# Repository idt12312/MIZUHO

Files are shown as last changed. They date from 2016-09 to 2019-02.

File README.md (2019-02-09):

# MIZUHOについて
## 概要
マイクロマウスの機体です。  

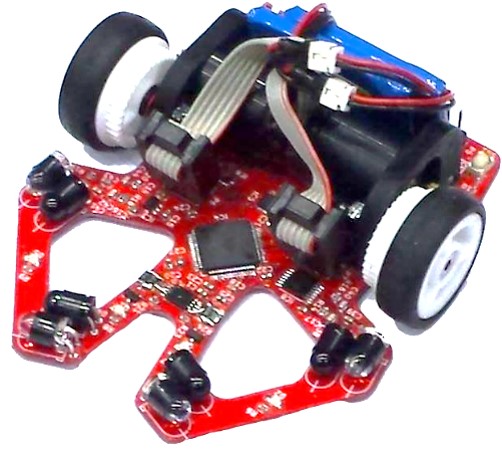
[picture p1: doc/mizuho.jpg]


第37回全日本マイクロマウス大会のクラッシック競技フレッシュマンクラスに出場しました。  
予選を通過し、決勝では11位のタイムで完走しました。

## 使用部品

| | |
|---|---|
| マイコン | STM32F405RGT |
| 6軸センサ | MPU6500 |
| モータドライバ | DRV8835 |
| フォトダイオード | SFH213FA |
| 赤外線LED | VSLY5850 |
| モーター | Faulhaber 1717+IEH2-1024 |
| バッテリー | Hyperion 1cel 120mA × 2  |

# 内容物
* pcb/ : kicadの基板データ
* firmware/ : stm32のファームウェア(eclipseのプロジェクトファイル)

# ファームウェアについて 
## 構成
↓の画像のような構成になっています。

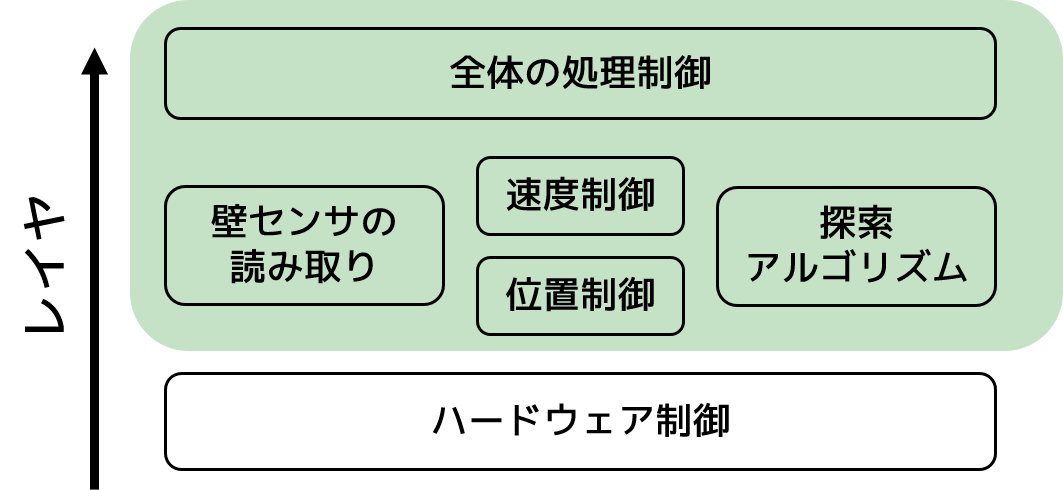
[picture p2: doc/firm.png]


[FreeRTOS](http://www.freertos.org/)を利用しています。  
上の画像の緑の色のついている部分がFreeRTOSのタスクになっています。  

## 制御の概要
だいたいこんな感じです。

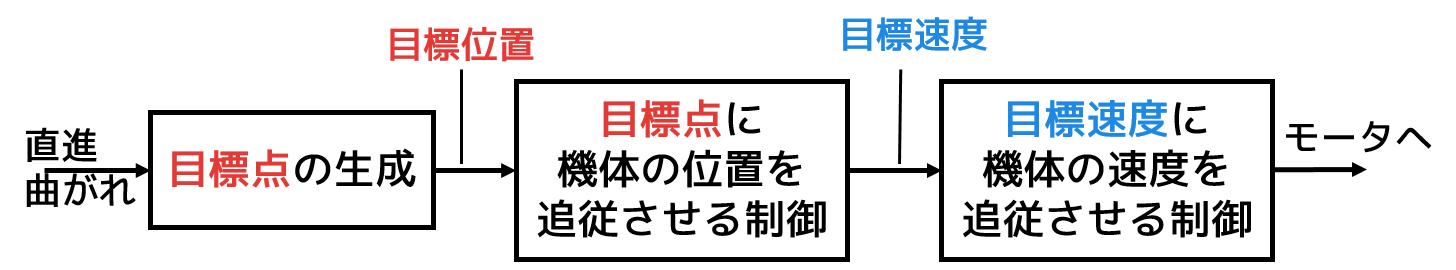
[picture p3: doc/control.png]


## 探索アルゴリズム
[以前作ったもの](https://github.com/idt12312/MazeSolver2015)を使用しています。

# 回路について
[回路図はここからpdfダウンロードできます。](./doc/micromouse2016.pdf)

## 壁センサ
壁センサは少し工夫したので説明しておきます。  
ロ技研内での技術交流のために作成したまとめ文章も置いておくので、よかったら見てください  
[研究報告書](https://github.com/idt12312/MIZUHO/blob/master/doc/docment.pdf)  

外乱を防ぐために赤外線LEDを変調して使っています。

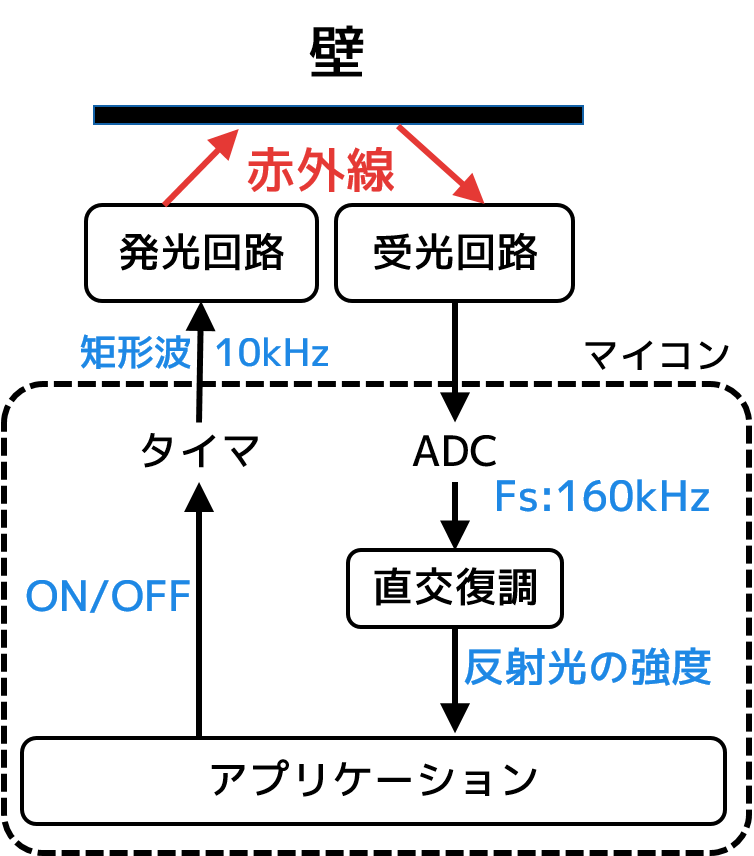
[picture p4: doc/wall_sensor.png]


受光した信号は直交復調に基づいて復調しています。  
計算自体はDFTをとある周波数についてだけ計算することと同じです。  

受光した信号を

、サンプリング周波数を

とします。  
ここでは

から周波数

成分の強度を計算するとします。  

まず

X[n] = \sum_{k=0}^{N-1}x[k]\exp({-j\frac{2 \pi nk}{N}})

を計算します。  

次に

の絶対値を計算することで  

に含まれる周波数

の振幅を得ることができます。

# 開発環境
## 基板
* 基板の外形はinventorで作成 -> dxfで出力
* 回路図・アートワークはKiCad 4.0.4-stableで作成

## STM32
* コンパイラ : GCC 4.9.3 (arm-none-eabi)
* デバッガ : GDB 7.8.0.20150604-cvs (arm-none-eabi)
* OpenOCD 0.9.0
* IDE : Eclipse
  * CDT
  * GNU ARM Eclipse plugin
* eclipseのプロジェクトの雛形はGNU ARM Eclipse pluginから自動生成されるものを使用
* STM32のStandard Peripheral Libraryを使用

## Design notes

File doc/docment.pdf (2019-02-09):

# MIZUHO(マイクロマウス)の開発 ～壁センサの新提案～

Cheese∗ @idt12312

2016.12.5

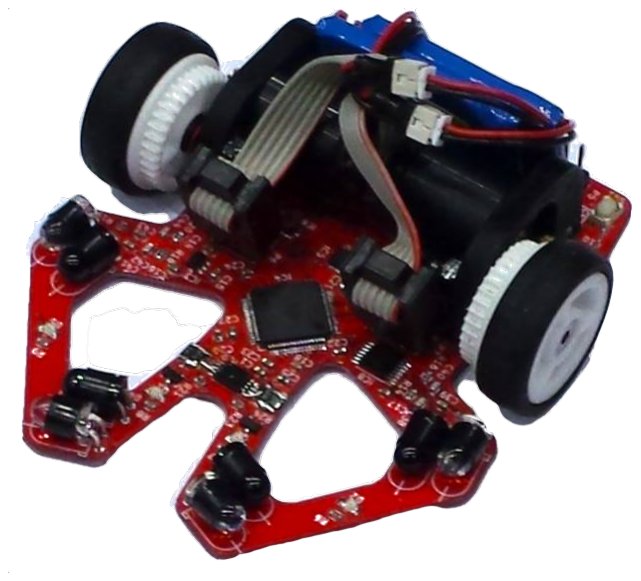
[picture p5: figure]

図 1: MIZUHO の外観

## 1 はじめに

マイクロマウスの競技のため, MIZUHO(図 1) とい う機体を製作した. マイクロマウスの機体の製作は初
めてであるため, 基本的にはよく知られたものを組み合 わせて製作をした. しかし, 唯一壁センサ周りに関して は既存のものを真似るだけではなく, 独自に開発を行っ た. そのため, 本報告書では独自に開発をした壁センサ について述べる.
マイクロマウスにおいて, 壁センサはフィールドに
ある壁の有無や壁との距離を計測するために使われ,
フィールドに対する絶対的な位置情報を取得できる唯
一のセンサである. そのため, 競技発足初期から現在に 至るまで, また初心者から上級者までほとんどの機体で 壁センサは利用されている. しかしネット上でも見ら
れる広く知られている壁センサの構成方法 [2] には後の 章で述べる問題点があるため, 新たな壁センサの構成方 法を開発するに至った.
ちなみに, MIZUHO の開発に関するソースコード, 基板の設計データ (KiCad) は全て github[1] にて公 開をしている. 製作過程や Tips などは id 研ブログ (http://idken.net) で公開をしているので, こちらも参 照していただきたい.

∗ロ技研内のマイクロマウスの機体の製作, 大会への出場を行う研 究室. 2016 年 12 月に設立.

## 2 壁センサの概要

MIZUHO はフィールドの壁情報を取得するために壁 センサを 4 つ搭載している. 左右の壁を見るために 2 つ, 前方の壁を見るために 2 つ搭載している (図 1). マイクロマウスの壁を見るセンサは赤外線 LED を利 用したものが最も一般的である. 赤外線 LED の光を壁 に当て, 反射して返ってくる光量を測定することで壁の 有無・壁との距離を計測することができる. なお, 光量 の計測にはフォトダイオードやフォトトランジスタを
使用されることが多い. しかしこの方法の問題点とし
て, 照明などの周囲の光の影響を受けやすいというもの が挙げられる.
この問題を解決するため, 照射する光を変調するとい
う手法が用いられている. 具体的には赤外線 LED を十 分に高い周波数で点滅させ, LED が ON になっている ときの受光した信号と OFF になっているときに受光し た信号の差をとる [2](以降従来手法と呼ぶ) というもの である. 会場の照明として水銀灯や蛍光灯があり, それ らは数 100Hz で点滅をしているため, 例えば数 kHz の 周波数で変調することで照明の影響を受けなくするこ
とができる. 変調方法として, LED を一定の周波数で 点滅させる方法や単純に LED を短いパルス状に点灯す るという方法が用いられている.
従来手法は信号の振幅を計測する手法であるが, 波形
がなまりすぎている場合や変調した周波数に近い (オー ダーが同じくらい) 外乱がある場合は精度よく計測をす ることができないことが予想される. そこで今回は光
を変調して発光, 受光する回路とその変調された信号の 強度を精度よく算出する方法を提案する.
提案するシステムである壁センサの関連の構成は図
2 のようになっている.
発光回路はマイコンから入力される信号に応じて
LED を点灯する. ここでは部品のばらつきによって 照射強度にばらつきがでない工夫がしてある. 受光回
路では, マイコンでの信号処理の前段階として 1 次の LPF と HPF を施しつつ, 信号を増幅している. マイコ ン内部では, 受光した信号を ADC を通して取り込み, 直交復調を用いることで特定の周波数の強度を算出し

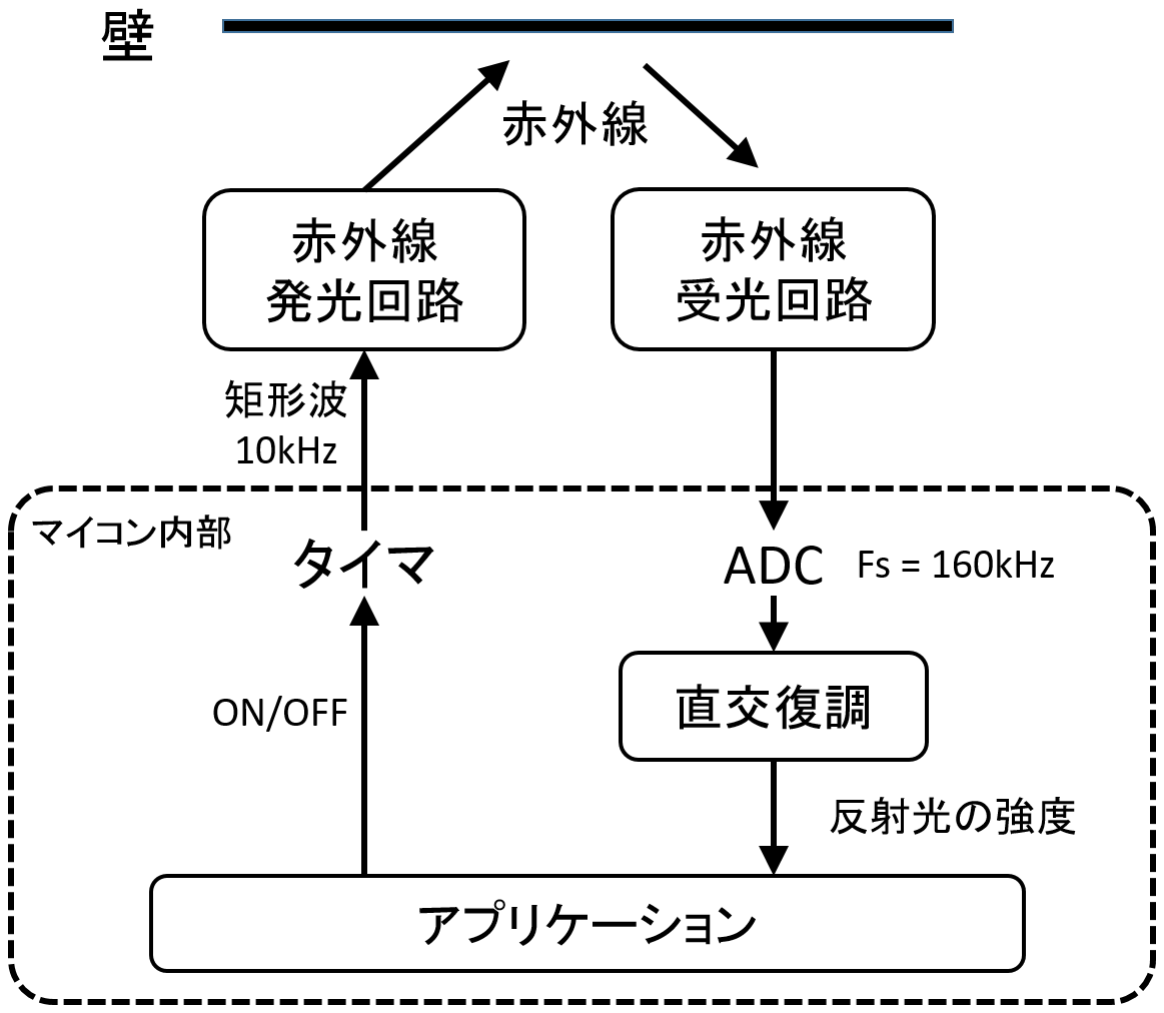
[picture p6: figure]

図 2: 壁センサのシステム構成

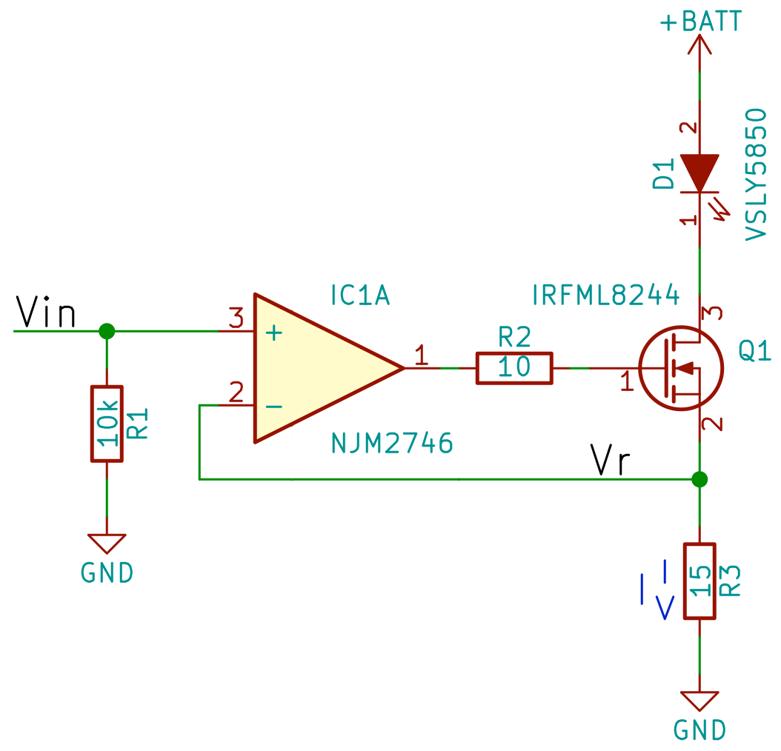
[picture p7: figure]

図 3: 赤外線発光回路

ている.
以降の章では発光回路, 受光回路, 直交復調の詳細に ついて述べる.

## 3 発光回路

MIZUHO の壁センサの発光回路には図 3 の回路を用 いた. この回路はオペアンプ, FET, R3 の抵抗で定電流 回路を構成している. この定電流回路により LED には 一定の電流が流れるため, 電源電圧の変動や LED の順 方向電圧などの部品によるばらつきの影響を受けない
ようにすることができる. なお, 実際には赤外線 LED を 2 個直列にしてこの回路を 2 セット用いて実装して いる.
LED に流れる電流はオペアンプの入力電圧 Vin に よってアナログ的に変化させることができる. オペア
ンプによって Vr = Vin になるように FET が駆動され るので, R3 には常に Vin の電圧が印加される. FET の ドレインからゲートにはほとんど電流が流れないため,
LED に流れる電流 I は

I =

V in
R3

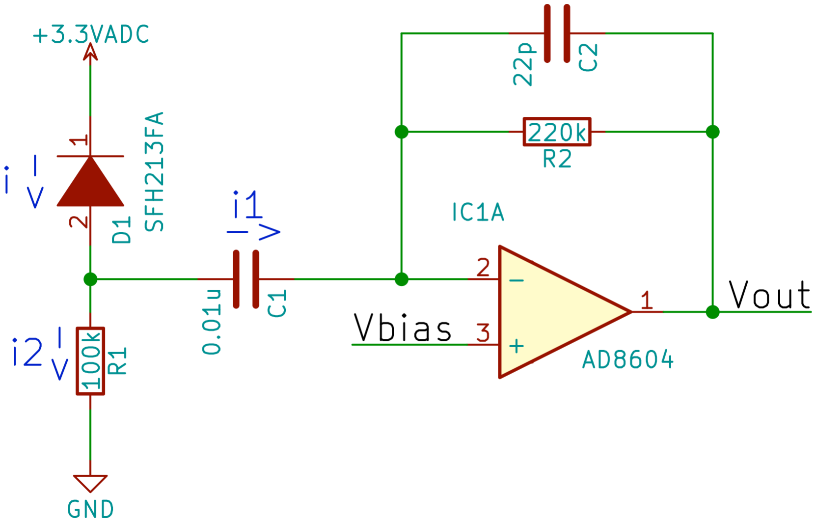
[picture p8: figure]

図 4: 赤外線受光回路

により決まる.
この回路を製作する際には次の 3 点に注意する必要
がある. 一つ目は抵抗での消費電力である. 抵抗では

V

2
r

R の電力が消費されることになるので, それに耐えら れる抵抗を選択する必要がある. ただし, 抵抗での消費 電力は実効電力で考えればよいため, Vin に矩形波や短 いパルスを入力する場合は V

2
r

R よりも少ない消費電力
に耐えれば十分である. 二つ目はオペアンプと FET で 構成されるフィドバックループの安定性についてであ
る. 図 3 のオペアンプの出力からオペアンプの-端子ま での伝達を考えると, 1. オペアンプの出力電位が上が る 2.FET のゲートソース間電圧が上がる 3.FET のド レイン電流が増える 4. 電流検出用抵抗の両端電圧が大 きくなる 5. オペアンプの-端子の電位が上がるという ループができている. 実際にはドレインと負荷の間の
配線によるインダクタンスや FET のゲート容量によっ てこのループに遅れ成分ができてしまうので, この遅
れを考慮してループが安定になるように部品を選定し
たり適切な位相補償を行うことが重要である. 三つ目
は LED の順方向電圧についてである. この回路が正常 に動作するためには, FET のドレインソース間に十分 (飽和領域で動作するように) に電圧がかかっている必 要がある. FET には電源電圧から LED の順方向電圧 と Vr(Vin) を引いた電圧がかかるので, それが十分に大 きくなるように設計をする必要がある.

## 4 受光回路

MIZUHO の壁センサの受光回路には図 4 の回路を用 いた. この回路ではフォトダーオードに流れる電流を
電圧に変換しつつ, 増幅, BPF としての機能も持って いる.
光を電子信号に変換するためにフォトダイオードを
使用している. フォトダイオード基本的にはダイオー
ドと同じ動作をし, 光を受けるとダイオードの逆方向に 電流を流すという性質がある. フォトトランジスタと
比較をすると, フォトトランジスタよりも感度が低いが 線型性, 応答速度の面で優れている [3]. 今回は高い周

波数成分を持つ変調した信号を受ける必要があるため
に, 応答速度の面からフォトダイオードを採用した.
フォトダイオードには, 逆バイアス電圧を掛けること
で応答速度, 感度がともに増加する性質があるため [3], 図 4 のような回路構成になっている.
フォトダイオードは受光した光の強度を電流に変換
するため, マイコンの ADC で読み取るためにこの電流 を電圧に変換する必要がある. 今回は I-V 変換回路と して図 4 中のオペアンプと R2 で構成されるものを利 用している.
この回路では光の強度を電圧情報に変換するだけで
はなく, 周波数フィルタも構成している. HPF は蛍光 灯などの外乱抑制のためではなく, 定常的 (0Hz) な環 境光やフォトダイオードの暗電流によってオペアンプ
の入力が飽和しないようにする働きをする. こうする
ことでオペアンプを飽和させることなく大きな増幅率
を達成することができる. LPF は後段のマイコンでの 信号処理のために, ADC のナイキスト周波数において 十分に信号の強度を下げる働きをする. 回路の周波数
特性と増幅率を解析するため, フォトダイオードに逆方 向に流れる電流を i とし, i からこの回路の出力 Vout ま での伝達関数を小信号解析によって求める. 小信号解
析をするため, 電源の+3.3VADC と Vbias は接地され ているものとして考える. まずは R1 と C1 に流れる電 流をそれぞれ i1, i2 とすると
i = i1 + i2 | (1)

という関係が成り立つ. オペアンプが理想的なオペア
ンプであるとするとオペアンプの-端子に電流は流れ込
まず, 電位は+端子と同じ 0V になる. そのため C1 に 流れた i2 は全て R2, C2 に流れることになる. このこと から,

i2 = −(

1
R2
+ C2s)vout | (2)

という関係が成り立つ. また, C1 のオペアンプ側は 0V であるので

R1i1 =

1
C1s
i2 | (3)

という関係が成り立つ. 式 (1)(2)(3) から vout と i の関 係を計算すると

vout = −

R1C1s
R1C1s + 1 1

1
R2C2s + 1 2

R2i (4)

のようになる. 式 (4) の 1 はよく知られている RC で 構成する HPF と同じ伝達関数である. ゆえに高周波域 (周波数が無限大) でのゲインは 1 でカットオフ周波数 は 1
2πR1C1 になる. また, 式 (4) の 2 は RC で構成され る LPF と同じ伝達関数である. ゆえに低周波域 (周波 数が 0) でのゲインは 1 で, カットオフ周波数は 1
2πR2C2
になる. 最後に, 式 (4) の R2 は上記 LPF と HPF で構

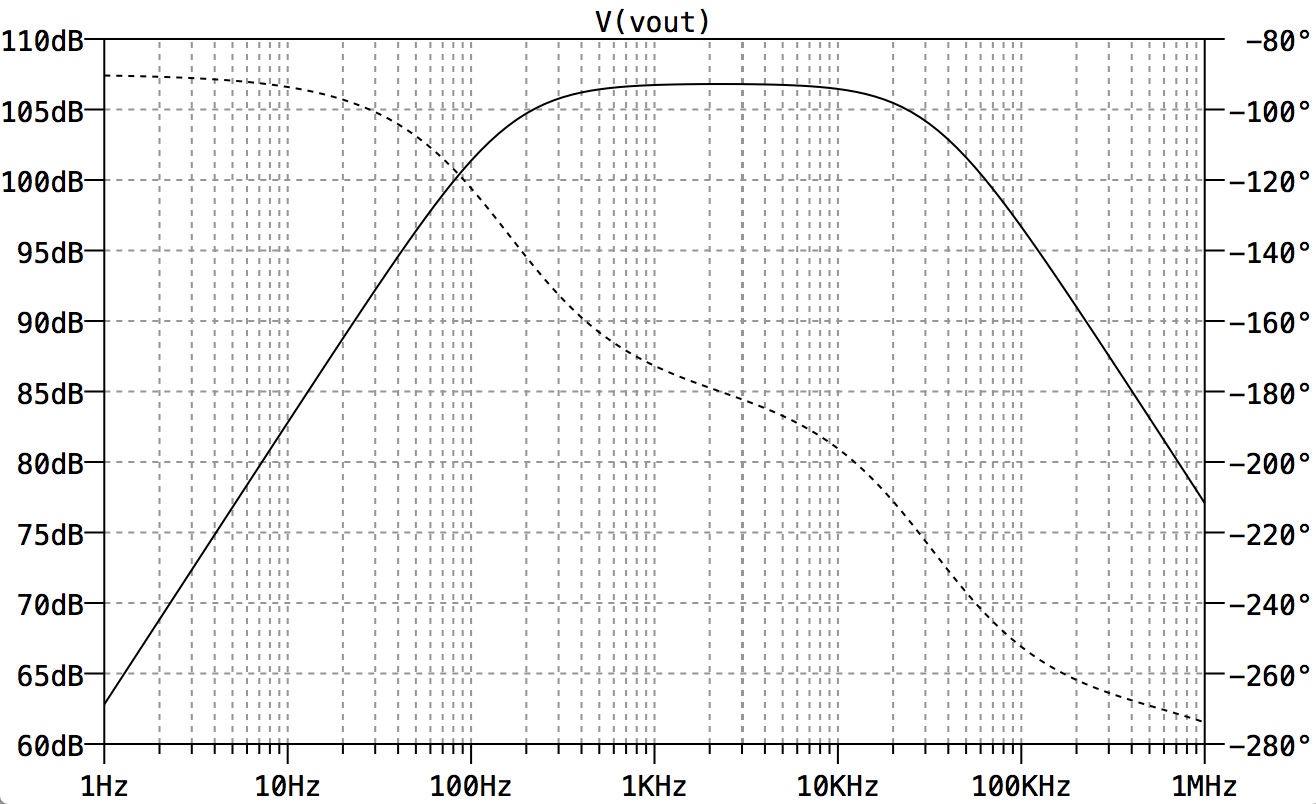
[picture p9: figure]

図 5: 受光回路の入力電流 → 出力電圧の周波数特性

成される BPF の通過域のゲインになっている. このよ うに式 (4) 中には LPF と HPF 両方の成分が含まれて いるが, それぞれ独立した部品のパラメータによって設 計することができるので, 所望のゲイン, HPF や LPF の特性を自由に設定することができる.
MIZUHO において実際に使用した部品定数は図 4 内 に記されているものである. 図 2 にある通り, 赤外線 LED は 10kHz の矩形波で駆動するため, 10kHz は通過 をさせる BPF になるようにした. 矩形波で駆動するの で 10kHz の奇数の整数倍で高調波がふくまれ, ADC の サンプルにおけるナイキスト周波数ではそれらの高調
波が抑えられている必要があるので, LPF は 10kHz の すぐ上にカットオフ周波数を持つように設計した. 全
体のゲインは実験により, マイクロマウスの壁がうまく 検出できるように飽和などに気をつけながら決定をし
た. ここでの HPF は先に述べた通り, 蛍光灯などの外 乱抑制のためではなく, 定常的 (0Hz) な環境光でオペ アンプの入力が飽和しないように 0Hz をカットできて さえいれば十分である. とはいえ低周波域をカットで
きることに越したことはないので, 10kHz あたりに影 響を与えない 100Hz あたりにカットオフ周波数を設定 した. 図 4 の部品定数を用いた時の実際の周波数応答 は図 5 のようになった. なお, この周波数応答の解析に は LTSpice を使用した.
この受光回路の出力をマイコンの ADC でサンプル
すると, 図 6 のような信号が得られた. ここでは赤外線 LED は 10kHz 矩形波で駆動し, ADC のフルレンジは 3.3V12bit, 160kHz で 64 サンプルをしている. 図 6 を みると, 信号が 2000 あたりを中心に振動している. こ れは受光信号が HPF で 0Hz 成分が消え, 図 4 の Vbias によって 1.65V のオフセットが乗っているからである.

## 5 直交復調

前章までで, マイコンに図 6 のような時系列信号を 取り込むことができた. 本章では, この時系列信号から 赤外線 LED の発した信号に起因するものだけを取り出

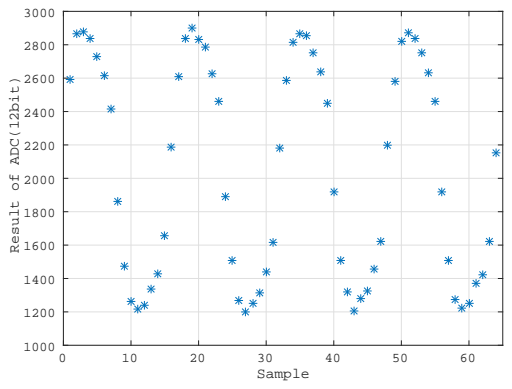
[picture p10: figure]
Sample; Result of ADC(12bit)

図 6: 受光した信号を ADC でサンプルした結果

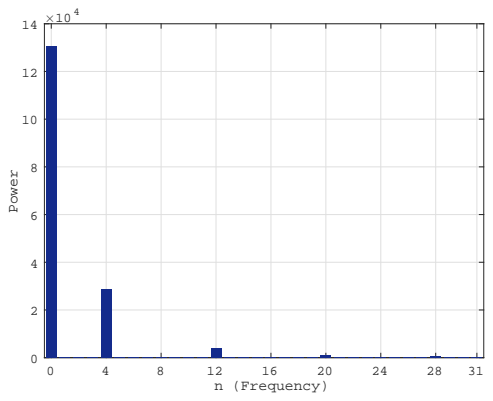
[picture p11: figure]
n (Frequency); Power

図 7: ADC でサンプルした信号の周波数分布

し, さらにその信号の強度を算出する方法について述
べる.
図 6 の信号の周波数分布をプロットすると図 7 のよ うになった. データ数は N = 64 で, サンプル周波数は Fs = 160kHz である. N 個の時系列信号を離散フーリ エ変換したので, 図 7 の横軸における 1 は Fs
N

[Hz] に相
当する. ゆえに図 7 の横軸の n というのは Fs
N

n[Hz] と
いう意味である.
図 7 によると 0Hz 以外では 10kHz(n = 4) のところ にピークが立っている. 赤外線 LED を 10kHz の矩形 波で駆動したことに起因すると考えられる. 矩形波で
駆動したため高調波も見られるが, 矩形波の振幅と基本 周波数 (10kHz) は比例するため, 今回は 10kHz 成分の みを取り出す方法を考える.
特定の周波数成分を取り出す方法として, 信号をフー
リエ変換をする方法が一般的に使われている. これは
フーリエ変換によって図 7 の周波数応答全体が得られ るので, n = 4 のところの強度のみを取り出せばよい. 時系列信号を x[k] ∈ R (k = 0, . . . , N − 1), x[k] を離 散フーリエ変換した信号を X[k] ∈ C (k = 0, . . . , N −1)

とすると, 離散フーリエ変換は

X[n] =

N

∑−1

k=0

x[k] exp(−j

2πnk
N

) (n = 0, . . . , N − 1)

(5)
で表される. X[n] は複素数で, 複素数の絶対値を計算 することでその周波数の強度を計算することができる.
DFT は式 (5) の計算を n = 0, . . . , N − 1 全てに対し て行うものであるが, 今回は全ての周波数の強度を計算 する必要はないので, 式 (5) を特定ひとつの n を計算す れば十分である. この計算はそこまで計算量が多くない (FFT よりも少ない) ので, マイコンで実行することも 可能である. 実際の MIZUHO では Fs = 10kHz, N = 64, n = 4 で計算をしている.
この方法は DFT の一部である, 式 (5) をとある n に ついて計算するものであると述べたが, 別の解釈をする こともできる. 式 (5) の n を固定し, exp を展開すると 次式のように書ける.

X[n] =

N

∑−1

k=0

(x[k] cos (−

2πnk
N

) + jx[k] sin (−

2πnk
N

))

(6)
式 (6) は時系列信号に対してお互いに直交する sin と cos と掛け算をしている. このように同じ周波数を持ち 直交する二つの正弦波を掛け, 掛け算をした正弦波と
同じ周波数を持つ成分の強度を取り出す操作のことを
直交復調という. 直交復調は電波を使った通信分野な
どで広く使われている. 今回紹介した方法はフーリエ
変換から式を導出したものであるが, 変調した信号で
LED を駆動し, 受光信号を復調するという意味で筆者 は直交復調と呼ぶのがふさわしいと考えている.
直交復調の実際の実装については github[1] にコード があるのでそちらを参照していただきたい.

## 6 おわりに

本報告書ではマイクロマウス機体の MIZUHO に使 用した壁センサについて, 発光回路, 受光回路, 直交復 調の 3 つの要素に分けて原理や設計方法を述べた. 提 案手法と既存の手法において, 実際の壁の検出性能など がどう違うのかについてはまだ比較ができていないの
で, その性能を検証をすることが今後の課題である.

## 参考文献

[1] idt12312/MIZUHO の github リ ポ ジ ト リ,

https://github.com/idt12312/MIZUHO

[2] RT Robot Shop, マイクロマウスのセンサについて

, http://www.rt-shop.jp/blog/archives/2139

[3] 谷 善平, 改訂 オプト・デバイス応用ノウハウ (1992), CQ 出版

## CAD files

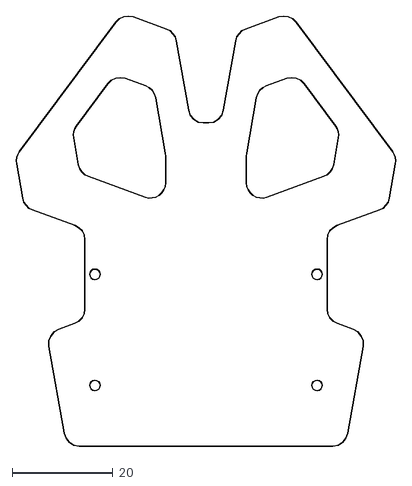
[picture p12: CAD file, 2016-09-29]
pcb/body.dxf
75.1 x 85.2

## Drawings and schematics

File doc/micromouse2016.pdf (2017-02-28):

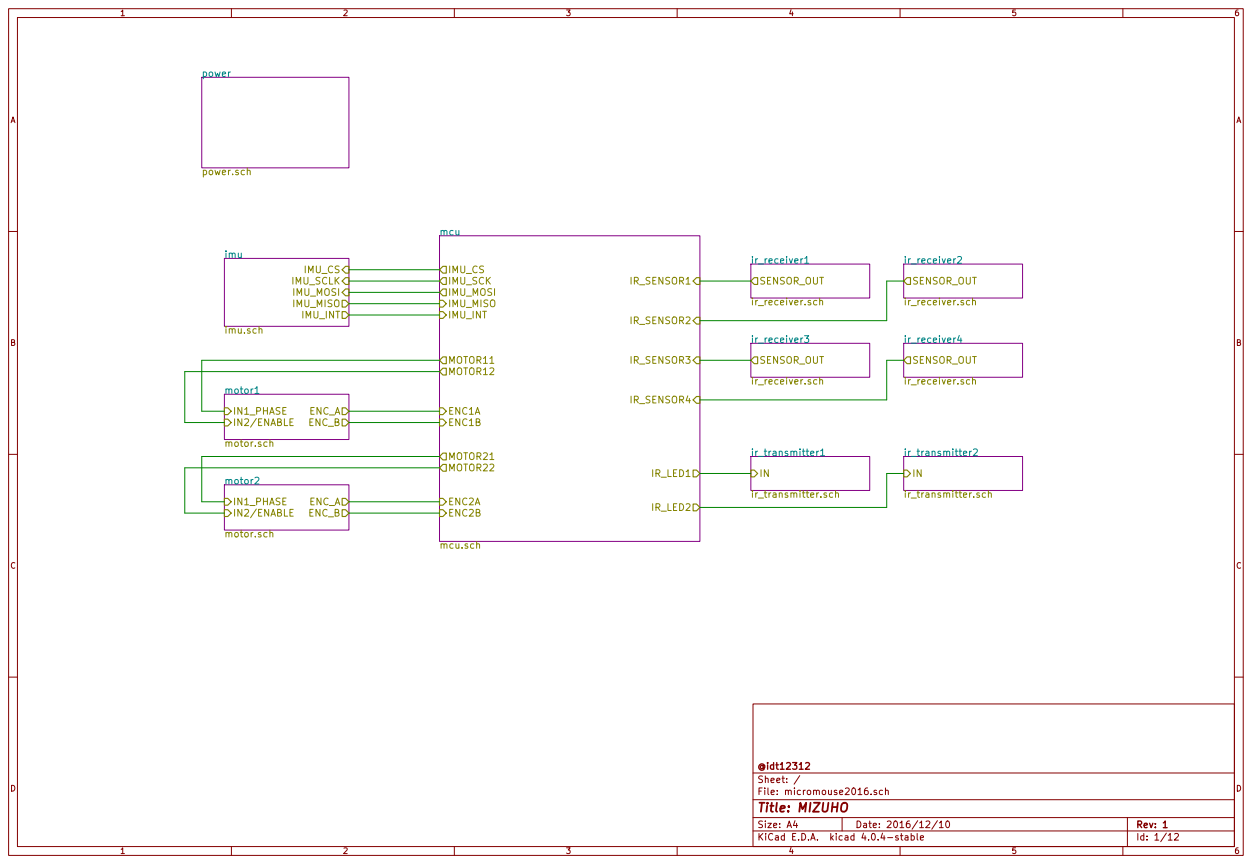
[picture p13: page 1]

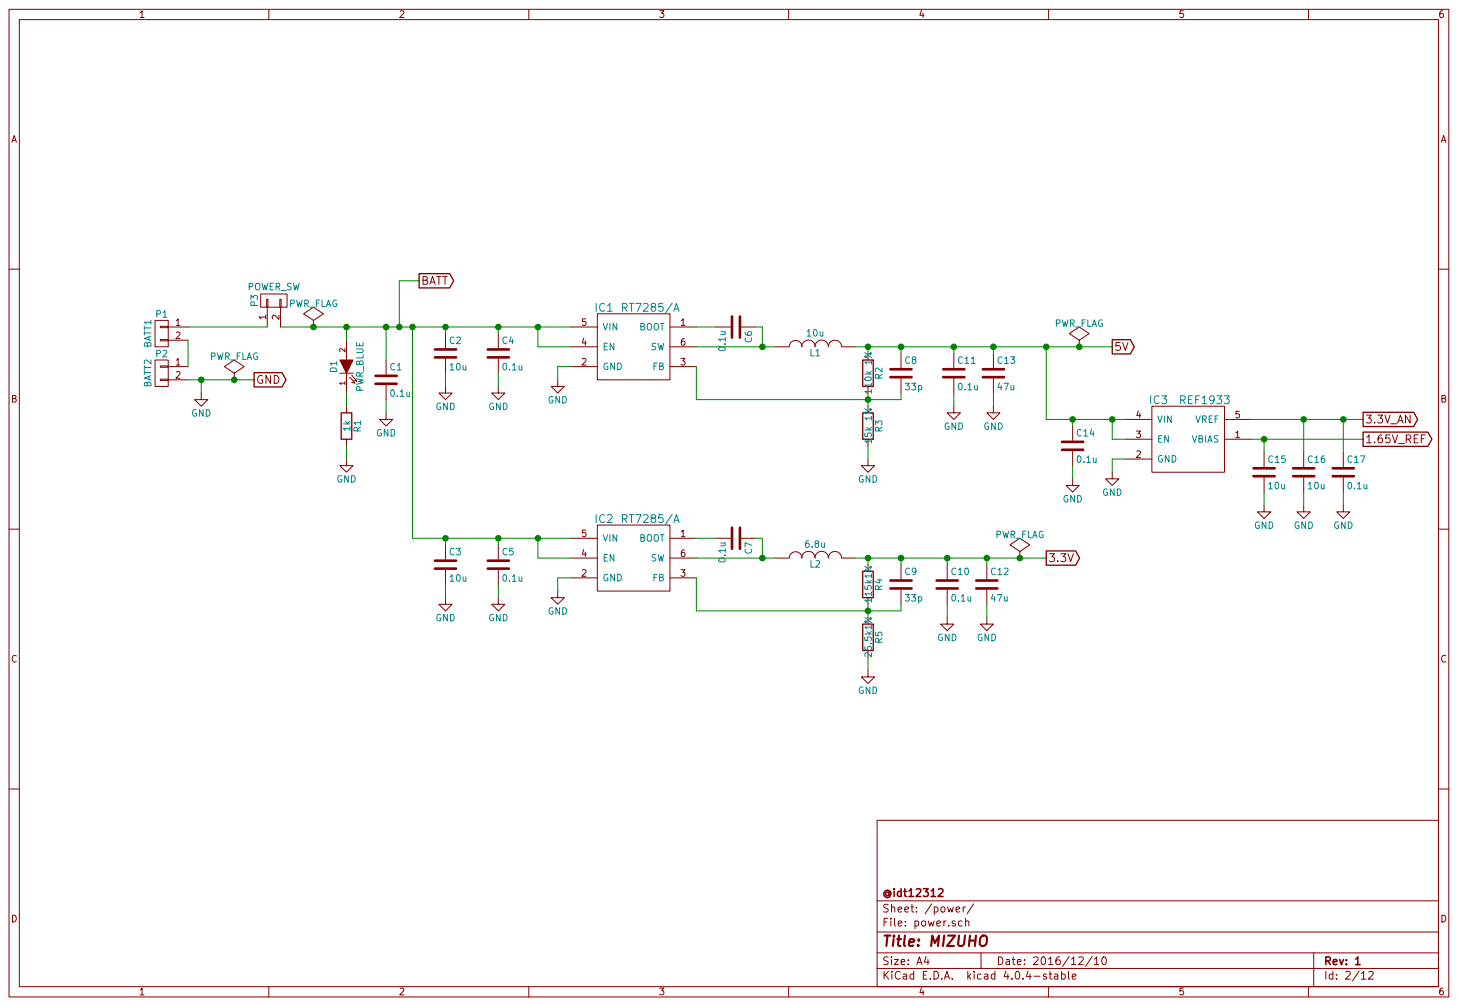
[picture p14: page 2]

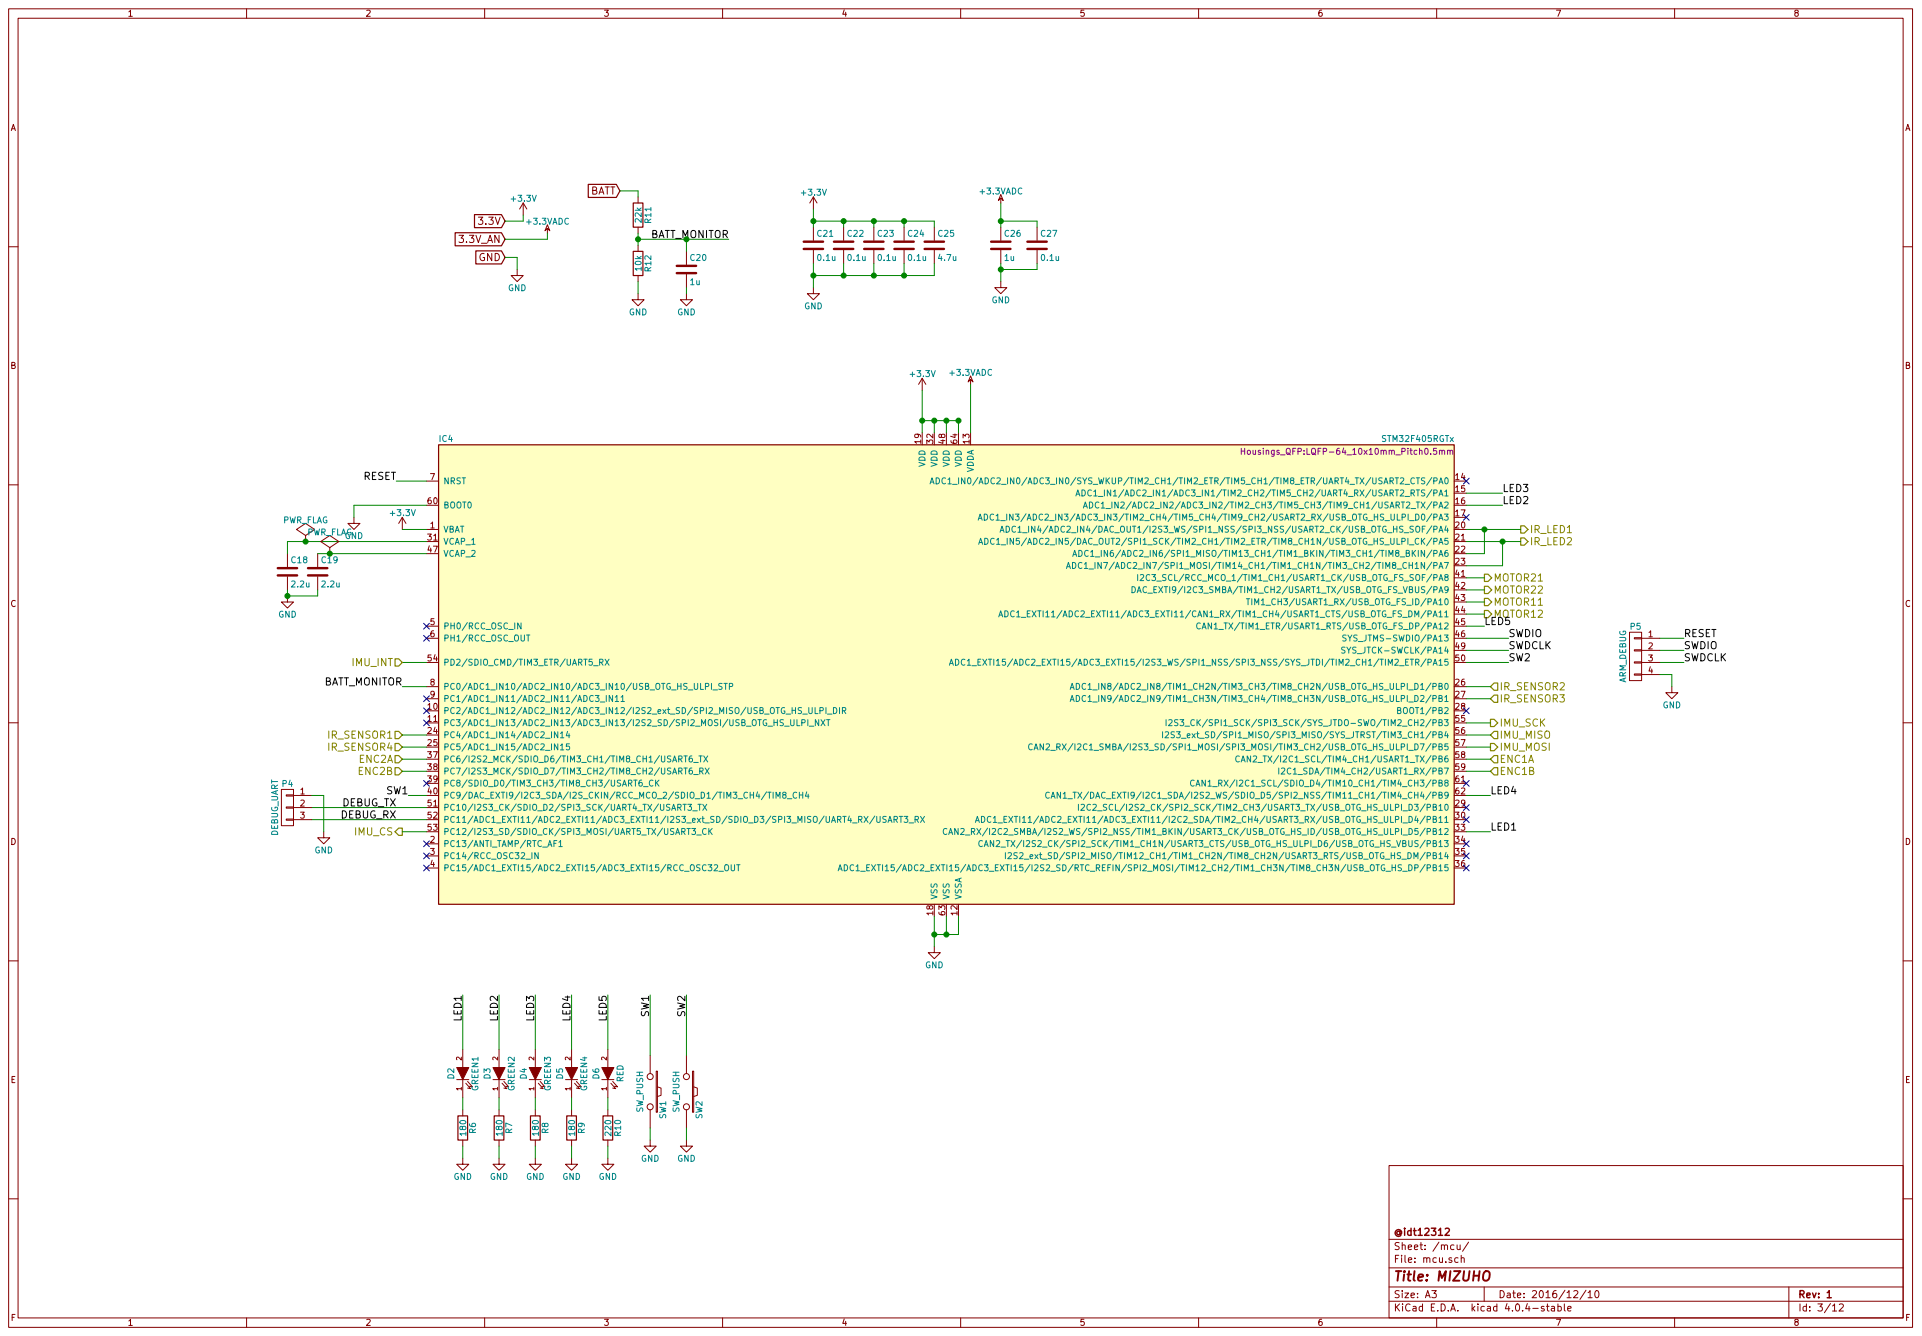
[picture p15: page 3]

File: mcu.sch Sheet: /mcu/ @idt12312

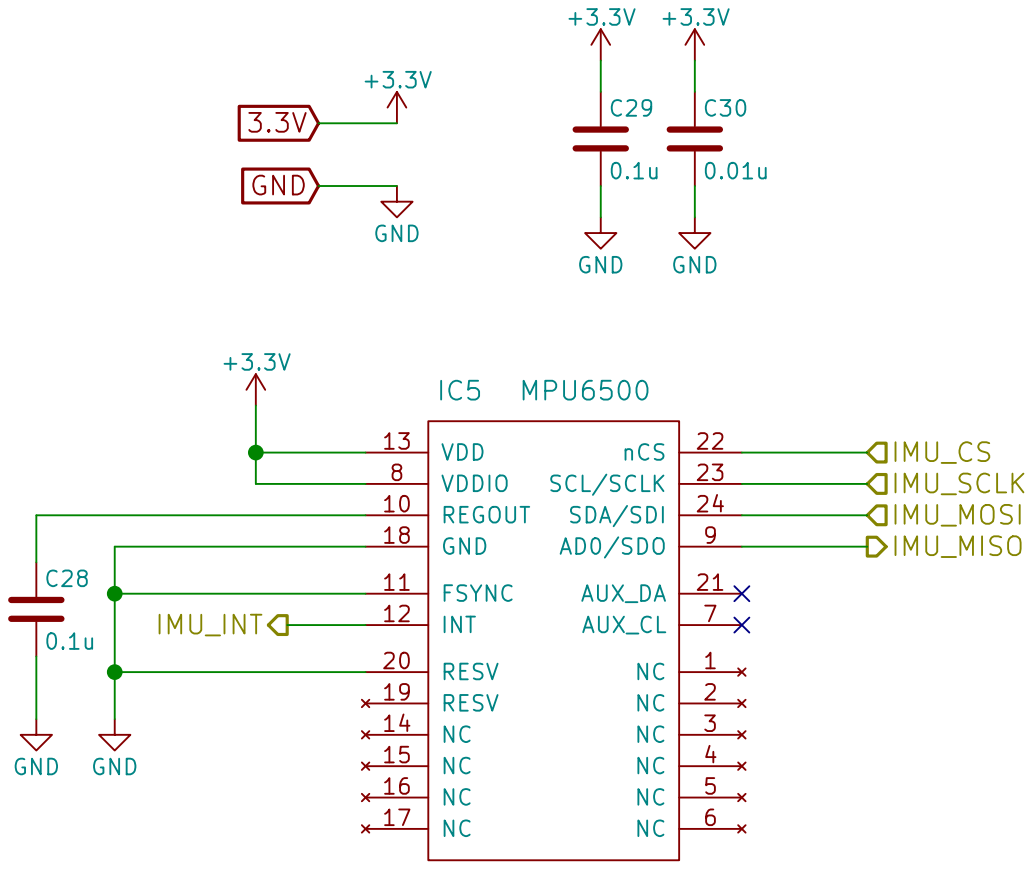
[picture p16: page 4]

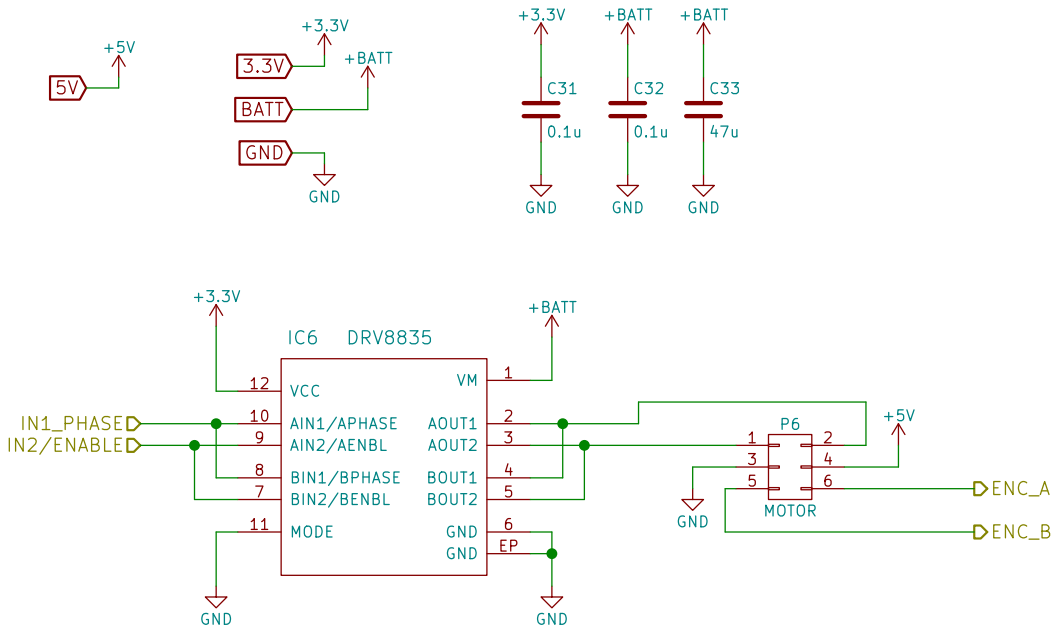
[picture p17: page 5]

File: motor.sch Sheet: /motor1/ @idt12312

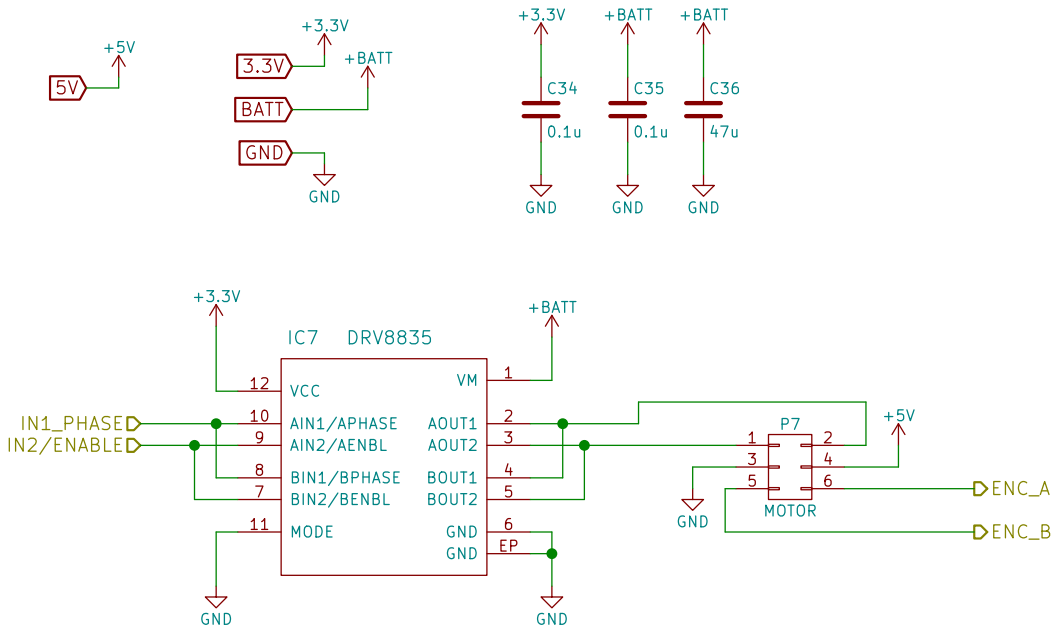
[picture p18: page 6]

File: motor.sch Sheet: /motor2/ @idt12312

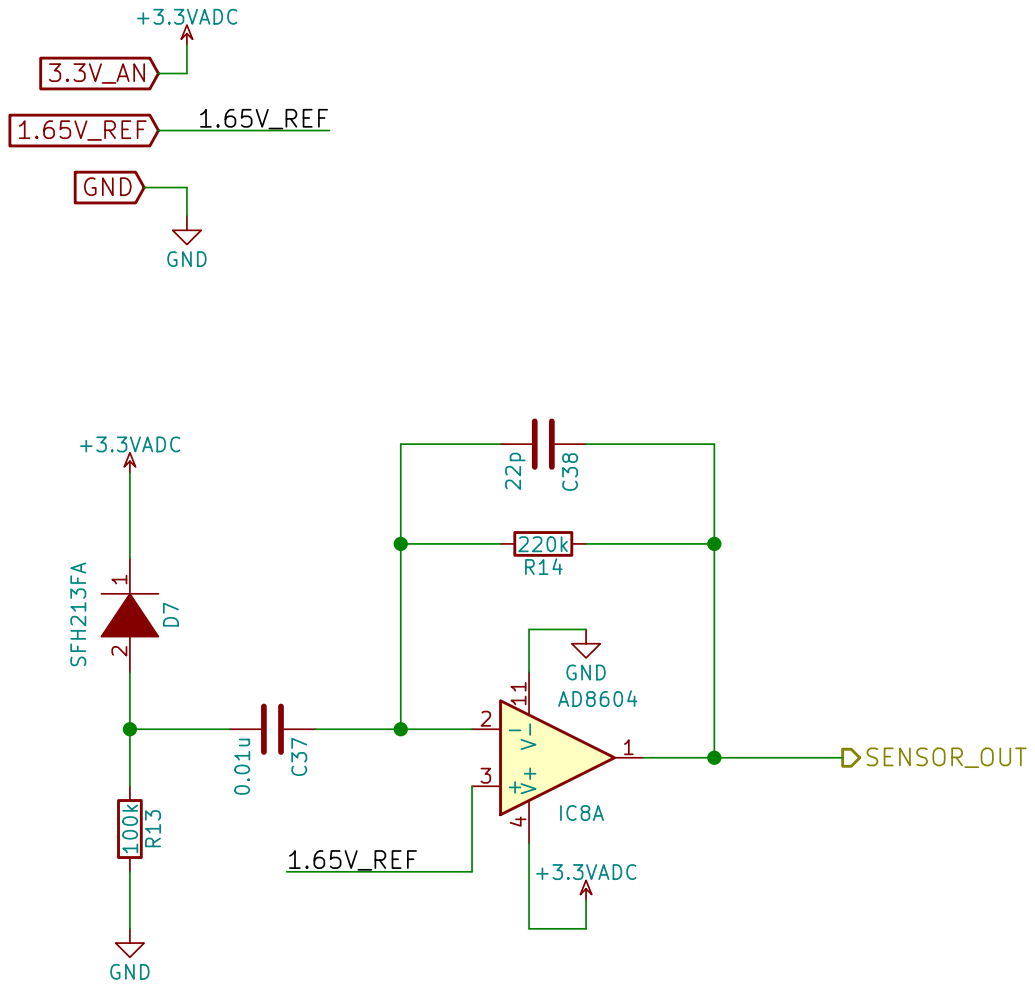
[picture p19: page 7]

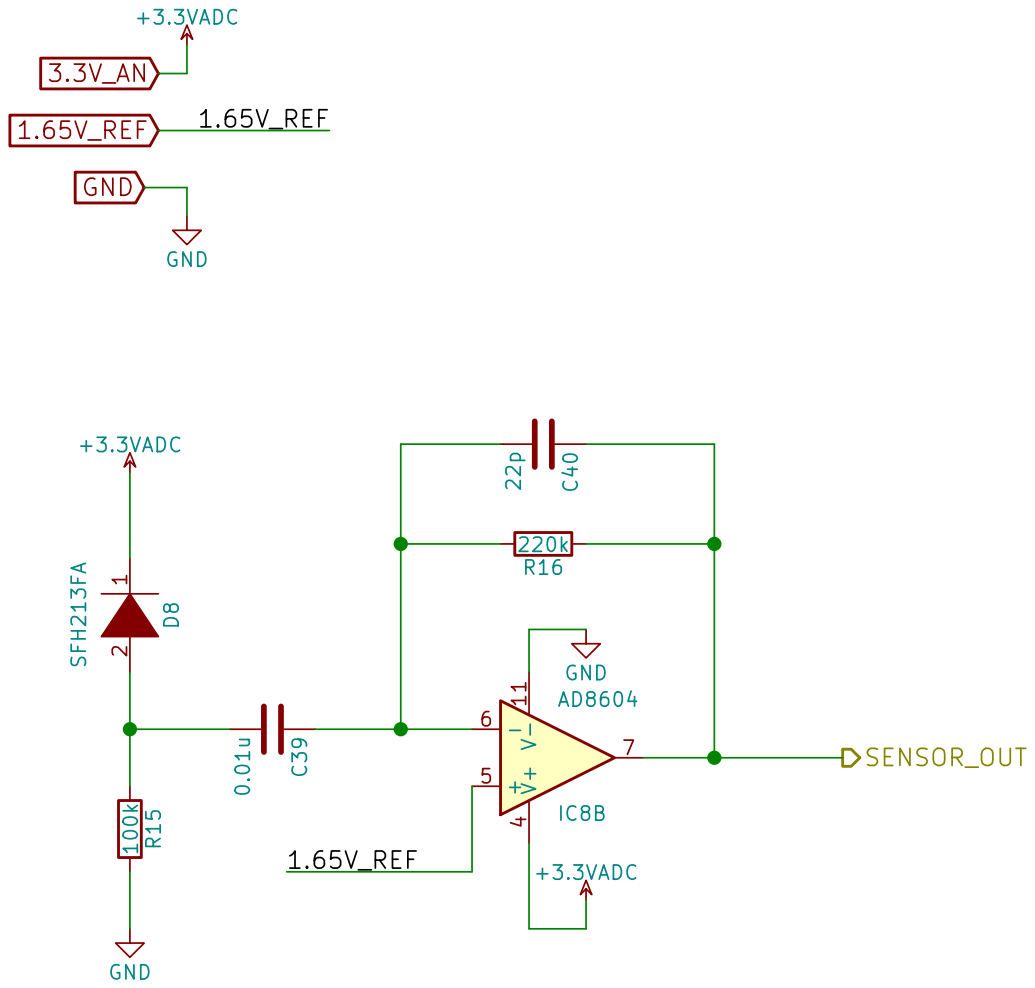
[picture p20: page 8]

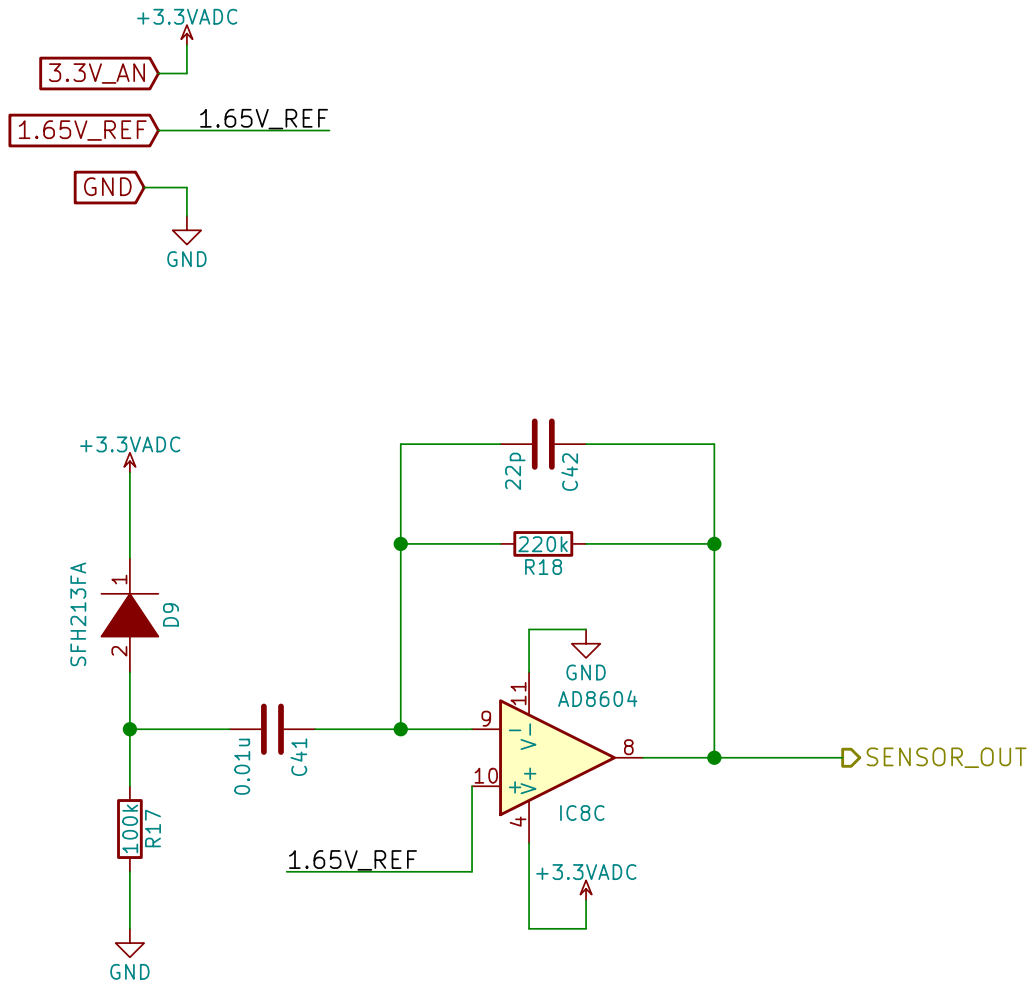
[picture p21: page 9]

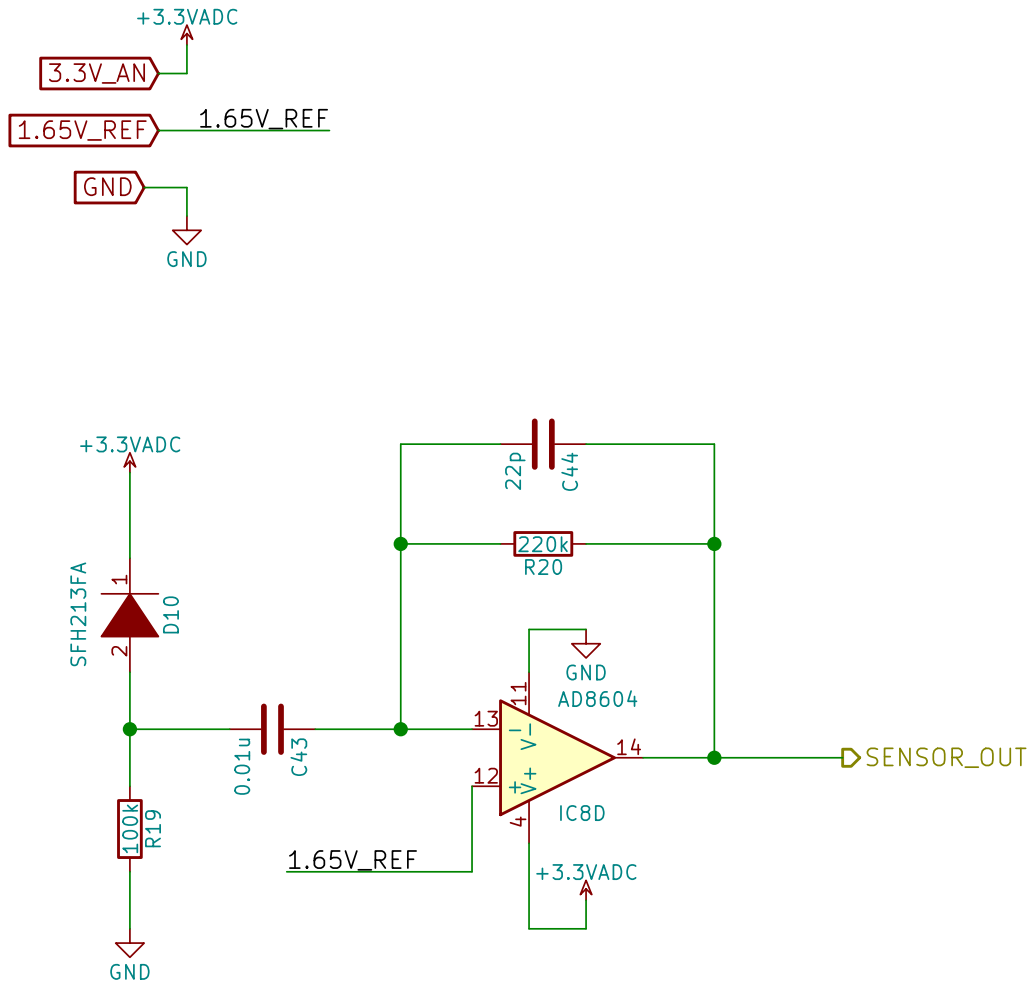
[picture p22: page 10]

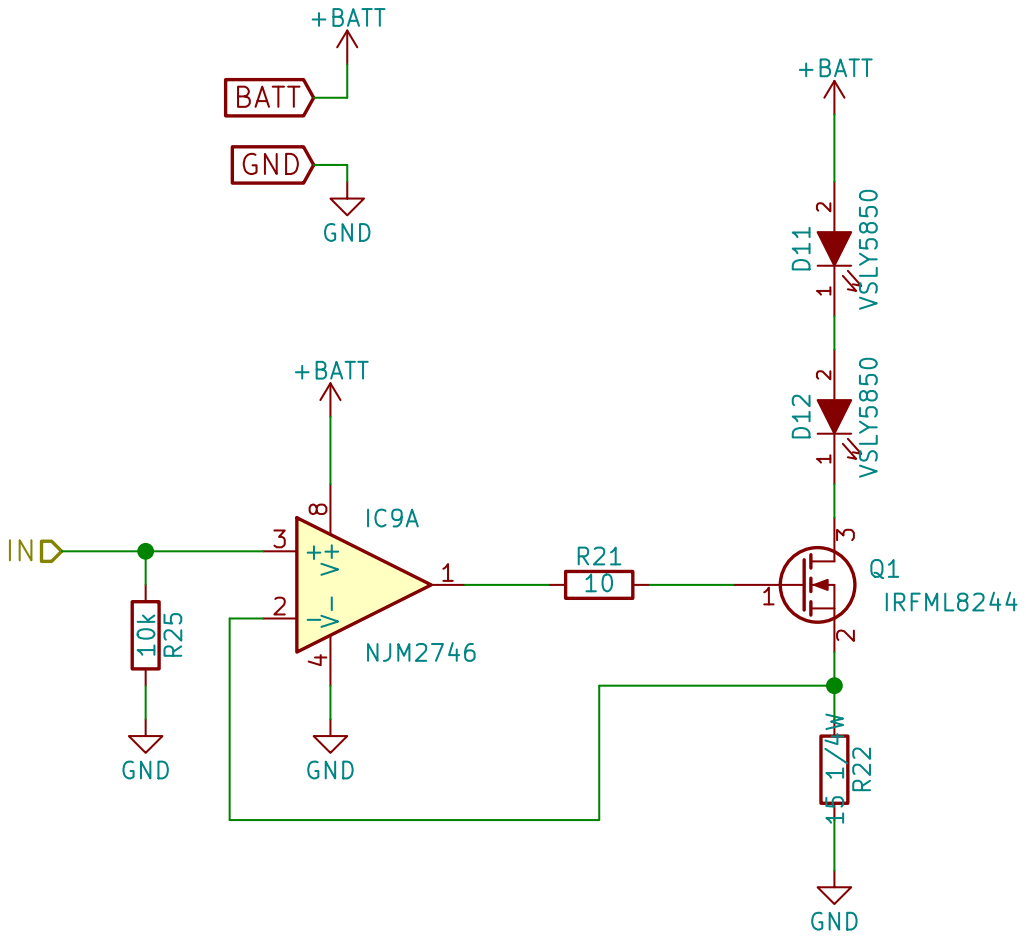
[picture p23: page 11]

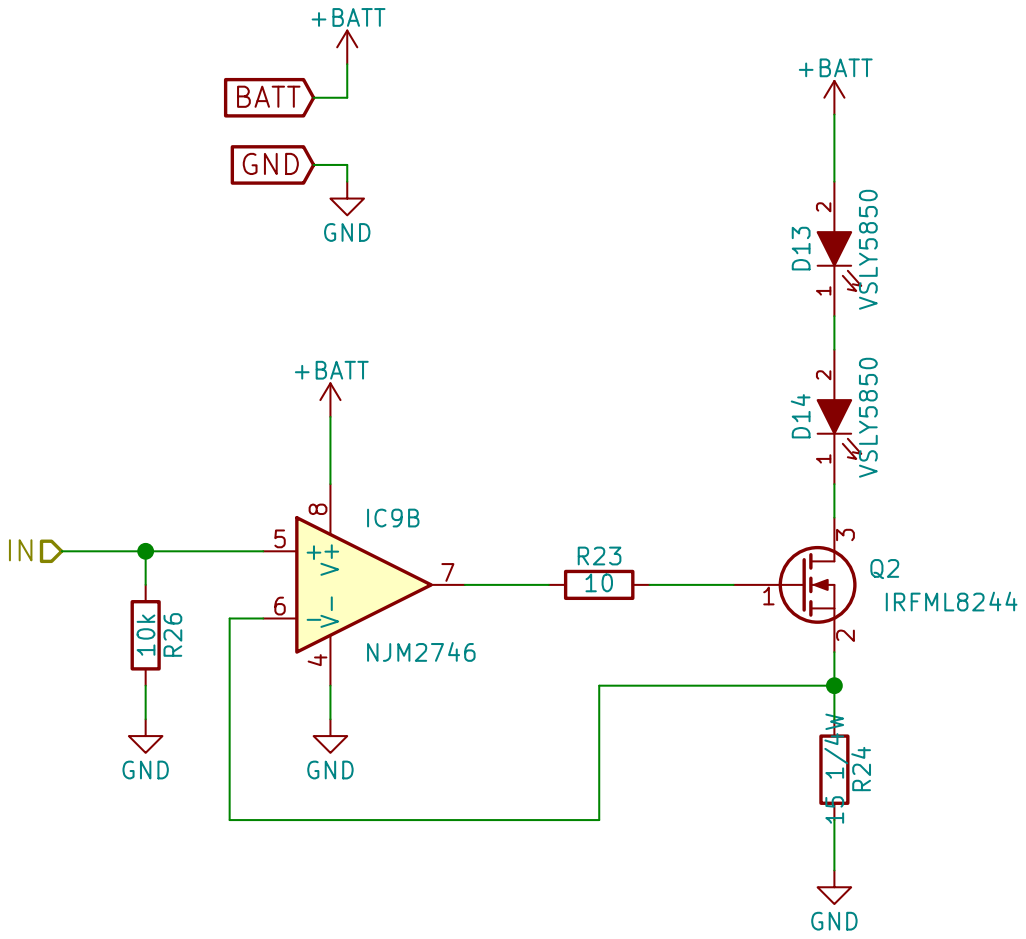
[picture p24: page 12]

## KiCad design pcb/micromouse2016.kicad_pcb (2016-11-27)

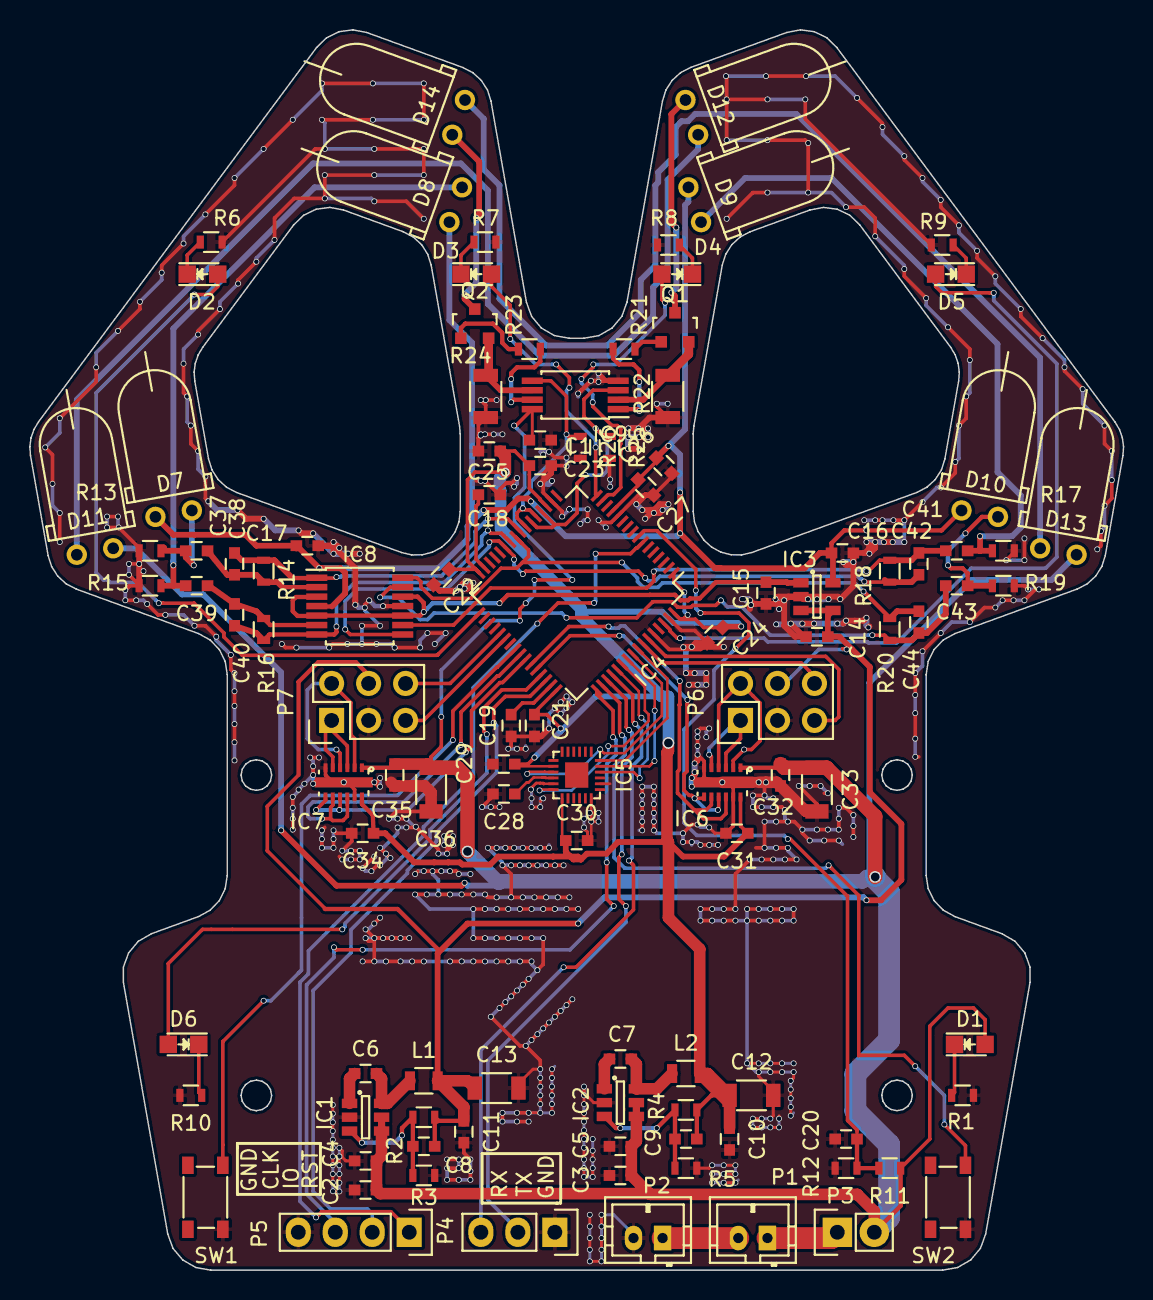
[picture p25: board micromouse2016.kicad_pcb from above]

Board: 2 copper layers, 75.1 x 85.2 mm, 106 parts (0 on the bottom side), 77 nets.

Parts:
C1, C4, C5, C6, C7, C10, C11, C14, C17, C21, C22, C23, C24, C27, C28, C29, C31, C32, C34, C35: 0.1u; C_0603
C2, C3, C15, C16: 10u; C_0603
C8, C9: 33p; C_0603
C12, C13, C33, C36: 47u; C_1206
C18, C19: 2.2u; C_0603
C20, C26: 1u; C_0603
C25: 4.7u; C_0603
C30, C37, C39, C41, C43: 0.01u; C_0603
C38, C40, C42, C44: 22p; C_0603
D1: PWR_BLUE; LED_0805
D2: GREEN1; LED_0805
D3: GREEN2; LED_0805
D4: GREEN3; LED_0805
D5: GREEN4; LED_0805
D6: RED; LED_0805
D7, D8, D9, D10: SFH213FA; LED_5mm_angle
D11, D12, D13, D14: VSLY5850; LED_5mm_angle
IC1, IC2: RT7285/A; SOT-23-6
IC3: REF1933; SOT-23-5
IC4: STM32F405RGTx; LQFP-64_10x10mm_Pitch0.5mm
IC5: MPU6500; QFN-24-1EP_3x3mm_Pitch0.4mm_HandSolder
IC6, IC7: DRV8835
IC8: AD8604; TSSOP-14_4.4x5mm_Pitch0.65mm
IC9: NJM2746; TSSOP-8_4.4x3mm_Pitch0.65mm
L1: 10u; R_0805
L2: 6.8u; R_0805
P1: BATT1; JST_PH_B2B-PH-K_02x2.00mm_Straight
P2: BATT2; JST_PH_B2B-PH-K_02x2.00mm_Straight
P3: POWER_SW; Pin_Header_Straight_1x02
P4: DEBUG_UART; Pin_Header_Straight_1x03
P5: ARM_DEBUG; Pin_Header_Straight_1x04
P6, P7: MOTOR; Pin_Header_Straight_2x03
Q1, Q2: IRFML8244; SOT-23
R1: 1k; R_0603
R2: 110k 1%; R_0603
R3: 15k 1%; R_0603
R4: 115k1%; R_0603
R5: 25.5k1%; R_0603
R6, R7, R8, R9: 180; R_0603
R10: 220; R_0603
R11: 22k; R_0603
R12, R25, R26: 10k; R_0603
R13, R15, R17, R19: 100k; R_0603
R14, R16, R18, R20: 220k; R_0603
R21, R23: 10; R_0603
R22, R24: 15 1/4W; R_1206
SW1, SW2: SW_PUSH; SKRPACE010

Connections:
1.65V_REF: C15.1, IC3.1, IC8.3, IC8.5, IC8.10, IC8.12
3.3V: C9.1, C10.1, C12.1, C21.1, C22.1, C23.1, C24.1, C25.1, C29.1, C30.1, C31.1, C34.1, IC4.1, IC4.19, IC4.32, IC4.48, IC4.64, IC5.8, IC5.13, IC6.12, IC7.12, L2.2, R4.1
3.3V_AN: C16.1, C17.1, C26.1, C27.1, D7.1, D8.1, D9.1, D10.1, IC3.5, IC4.13, IC8.4
5V: C8.1, C11.1, C13.1, C14.1, IC3.3, IC3.4, L1.2, P6.4, P7.4, R2.1
/imu/IMU_CS: IC4.53, IC5.22
/imu/IMU_INT: IC4.54, IC5.12
/imu/IMU_MISO: IC4.56, IC5.9
/imu/IMU_MOSI: IC4.57, IC5.24
/ir_transmitter1/IN: IC4.20, IC4.22, IC9.3, R25.1
/ir_transmitter2/IN: IC4.21, IC4.23, IC9.5, R26.1
/mcu/BATT_MONITOR: C20.1, IC4.8, R11.2, R12.1
/mcu/DEBUG_RX: IC4.52, P4.3
/mcu/DEBUG_TX: IC4.51, P4.2
/mcu/ENC1A: IC4.58, P6.6
/mcu/ENC1B: IC4.59, P6.5
/mcu/ENC2A: IC4.37, P7.6
/mcu/ENC2B: IC4.38, P7.5
/mcu/IMU_SCK: IC4.55, IC5.23
/mcu/IR_SENSOR1: C38.1, IC4.24, IC8.1, R14.1
/mcu/IR_SENSOR2: C40.1, IC4.26, IC8.7, R16.1
/mcu/IR_SENSOR3: C42.1, IC4.27, IC8.8, R18.1
/mcu/IR_SENSOR4: C44.1, IC4.25, IC8.14, R20.1
/mcu/LED1: D2.2, IC4.33
/mcu/LED2: D3.2, IC4.16
/mcu/LED3: D4.2, IC4.15
/mcu/LED4: D5.2, IC4.62
/mcu/LED5: D6.2, IC4.45
/mcu/RESET: IC4.7, P5.1
/mcu/SW1: IC4.40, SW1.1
/mcu/SW2: IC4.50, SW2.1
/mcu/SWDCLK: IC4.49, P5.3
/mcu/SWDIO: IC4.46, P5.2
/motor1/IN1_PHASE: IC4.43, IC6.8, IC6.10
/motor1/IN2/ENABLE: IC4.44, IC6.7, IC6.9
/motor2/IN1_PHASE: IC4.41, IC7.8, IC7.10
/motor2/IN2/ENABLE: IC4.42, IC7.7, IC7.9
BATT: C1.1, C2.1, C3.1, C4.1, C5.1, C32.1, C33.1, C35.1, C36.1, D1.2, D11.2, D13.2, IC1.4, IC1.5, IC2.4, IC2.5, IC6.1, IC7.1, IC9.8, P3.2, R11.1
GND: C1.2, C2.2, C3.2, C4.2, C5.2, C10.2, C11.2, C12.2, C13.2, C14.2, C15.2, C16.2, C17.2, C18.2, C19.2, C20.2, C21.2, C22.2, C23.2, C24.2, C25.2, C26.2, C27.2, C28.2, C29.2, C30.2, C31.2, C32.2, C33.2, C34.2, C35.2, C36.2, IC1.2, IC2.2, IC3.2, IC4.12, IC4.18, IC4.60, IC4.63, IC5.11, IC5.18, IC5.20, IC6.6, IC6.11, IC6.EP, IC7.6, IC7.11, IC7.EP, IC8.11, IC9.4, P2.2, P4.1, P5.4, P6.3, P7.3, R1.2, R3.2, R5.2, R6.2, R7.2, R8.2, R9.2, R10.2, R12.2, R13.2, R15.2, R17.2, R19.2, R22.2, R24.2, R25.2, R26.2, SW1.2, SW2.2
unnamed: C6.1, IC1.6, L1.1
unnamed: C6.2, IC1.1
unnamed: C7.1, IC2.6, L2.1
unnamed: C7.2, IC2.1
unnamed: C8.2, IC1.3, R2.2, R3.1
unnamed: C9.2, IC2.3, R4.2, R5.1
unnamed: C18.1, IC4.31
unnamed: C19.1, IC4.47
unnamed: C28.1, IC5.10
unnamed: C37.1, C38.2, IC8.2, R14.2
unnamed: C37.2, D7.2, R13.1
unnamed: C39.1, C40.2, IC8.6, R16.2
unnamed: C39.2, D8.2, R15.1
unnamed: C41.1, C42.2, IC8.9, R18.2
unnamed: C41.2, D9.2, R17.1
unnamed: C43.1, C44.2, IC8.13, R20.2
unnamed: C43.2, D10.2, R19.1
unnamed: D1.1, R1.1
unnamed: D2.1, R6.1
unnamed: D3.1, R7.1
unnamed: D4.1, R8.1
unnamed: D5.1, R9.1
unnamed: D6.1, R10.1
unnamed: D11.1, D12.2
unnamed: D12.1, Q1.3
unnamed: D13.1, D14.2
unnamed: D14.1, Q2.3
unnamed: IC6.2, IC6.4, P6.2
unnamed: IC6.3, IC6.5, P6.1
unnamed: IC7.2, IC7.4, P7.2
unnamed: IC7.3, IC7.5, P7.1
unnamed: IC9.1, R21.1
unnamed: IC9.2, Q1.2, R22.1
unnamed: IC9.6, Q2.2, R24.1
unnamed: IC9.7, R23.1
unnamed: P1.1, P3.1
unnamed: P1.2, P2.1
unnamed: Q1.1, R21.2
unnamed: Q2.1, R23.2

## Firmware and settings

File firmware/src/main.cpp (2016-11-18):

#include "stm32f4xx.h"
#include <cstdio>

#include "FreeRTOS.h"
#include "task.h"

#include "uart.h"
#include "enc.h"
#include "motor.h"
#include "spi.h"
#include "mpu6500.h"
#include "irsensor.h"
#include "motor.h"
#include "led_button.h"
#include "battery_monitor.h"

#include "BlinkLedTask.h"
#include "BatteryMonitorTask.h"
#include "WallDetectTask.h"
#include "MotorControlTask.h"
#include "MotionControlTask.h"
#include "TopTask.h"
#include "ButtonTask.h"

static BlinkLedTask blink_led_task(LED_5);
static BatteryMonitorTask battery_monitor_task;
static WallDetectTask wall_detect_task;
static MotorControlTask motor_control_task;
static MotionControlTask motion_control_task;
static TopTask top_task;
static ButtonTask button_task;

void* __dso_handle = 0;

static void peripheral_init()
{
	// 割り込み優先度をpre-emption priorityに4bit割り当てる
	NVIC_PriorityGroupConfig(NVIC_PriorityGroup_4);

	Led_init();
	Button_init();
	Uart_init();
	Enc_init();
	Spi_init();
	MPU6500_init();
	BatteryMonitor_init();

	// TODO:irsensro -> motorの順に初期化しないとmotorが動かなくなる
	IrSensor_init();
	Motor_init();

	// デバッガによって処理が停止したとき
	// モータのタイマ, ADCのトリガとなるタイマ, LEDのPWM用タイマを停止する
	DBGMCU_Config(DBGMCU_STOP, ENABLE);
	DBGMCU_APB1PeriphConfig(DBGMCU_TIM1_STOP, ENABLE);
	DBGMCU_APB1PeriphConfig(DBGMCU_TIM2_STOP, ENABLE);
	DBGMCU_APB2PeriphConfig(DBGMCU_TIM3_STOP, ENABLE);
}


static void tasks_init()
{
	blink_led_task.create_task();
	battery_monitor_task.create_task();
	wall_detect_task.create_task();
	motor_control_task.create_task();
	motion_control_task.create_task();
	top_task.create_task();
	button_task.create_task();

	motion_control_task.set_motor_control_task(&motor_control_task);
	motion_control_task.set_wall_detec_task(&wall_detect_task);

	top_task.set_motor_control_task(&motor_control_task);
	top_task.set_motion_control_task(&motion_control_task);
	top_task.set_wall_detect_task(&wall_detect_task);
	top_task.set_blink_led_task(&blink_led_task);

	button_task.set_motor_control_task(&motor_control_task);
}


int main()
{
	peripheral_init();
	std::printf("peripheral initialization is completed\n");

	tasks_init();

	std::printf("Start FreeRTOS Scheduler\n");
	vTaskStartScheduler();

	while (1);
}

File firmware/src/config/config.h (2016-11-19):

/*
 * config.h
 *
 *  Created on: 2016/10/31
 *      Author: idt12312
 */

#ifndef CONFIG_H_
#define CONFIG_H_


/************************************************
 * デバッグ用の設定
 ***********************************************/
#define ODOMETRY_USE_GYRO				1
#define PRINT_WALL_SENSOR_RAW_VALUE		0
#define ENABLE_BATTERY_MONITOR_ABORT	0
#define ENABLE_BATTERY_MONITOR_PRINT	0


/************************************************
 * マシンの物理的パラメータ
 ***********************************************/
#define MACHINE_WHEEL_RADIUS	0.01237f
// 中心からタイヤまでの距離
#define MACHINE_TREAD_WIDTH 	0.03289f
#define MACHINE_ENC_CNT_PER_ROT	(1024*4*4)
#define MACHINE_MOTOR_VOLTAGE	7.6f

#define MACHINE_AXLE_TO_TAIL	0.034f
#define MACHINE_TAIL_COMP_LEN	0.015f


/************************************************
 * マシンの走行パラメータ
 ***********************************************/
#define WALL_DETECT_POINT				0.005f
#define STOP_TIME_AFTER_MOTION			50

#define SEARCH_STRAIGHT_DEFAULT_VELOCITY		0.3f
#define SEARCH_STRAIGHT_MAX_VELOCITY			0.31f
#define SEARCH_STRAIGHT_ACCERALATION			1.0f
#define SEARCH_PIVOT_ROTATION_VELOCITY			10.0f
#define SEARCH_PIVOT_ROTATION_ACCERALATION		30.0f
#define SEARCH_SLALOM_VELOCITY					0.3f
#define SEARCH_SLALOM_ROTATION_VELOCITY		7.0f
#define SEARCH_SLALOM_ROTATION_ACCERALATION	50.0f

#define FAST_STRAIGHT_DEFAULT_VELOCITY		0.3f
#define FAST_STRAIGHT_MAX_VELOCITY			0.6f
#define FAST_STRAIGHT_ACCERALATION			2.0f
#define FAST_SLALOM_VELOCITY				0.3f
#define FAST_SLALOM_ROTATION_VELOCITY		7.0f
#define FAST_SLALOM_ROTATION_ACCERALATION	50.0f


/************************************************
 * フィールドの物理的パラメータ
 ***********************************************/
#define BLOCK_SIZE	0.18f


/************************************************
 * バッテリー監視タスクの設定
 ***********************************************/
#define BATTERY_MONITOR_TASK_PRIORITY	4
#define BATTERY_MONITOR_TASK_PERIOD		2000
#define BATTERY_MONITOR_TASK_STACK_SIZE 256
#define BATTERY_MONITOR_AVE_CNT			5
#define BATTERY_MONITOR_ALERT_THREHOLD	7.3f
#define ADC_TO_BATTERY_VOLTAGE(x)		((float)x / 4096.0f * 3.3f * 3.0f)


/************************************************
 * 壁検出タスクの設定
 ***********************************************/
#define WALL_DETECT_TASK_PRIORITY		2
#define WALL_DETECT_TASK_PERIOD			5
#define WALL_DETECT_TASK_STACK_SIZE		512
#define WALL_DETECT_RL_THREHOLD			3300
#define WALL_DETECT_FRONT_THRETHOLD_NOSIDE		3500
#define WALL_DETECT_FRONT_THRETHOLD_WITH_SIDE		3500
#define WALL_DETECT_CNT					2
#define WALL_OFFSET_CNT					100

/************************************************
 * モータ制御(姿勢制御)の設定
 ***********************************************/
#define MOTOR_CONTROL_TASK_PRIORITY		1
#define MOTOR_CONTROL_TASK_PERIOD		1
#define MOTOR_CONTROL_TASK_PERIOD_SEC	((float)MOTOR_CONTROL_TASK_PERIOD/1000.0f)
#define MOTOR_CONTROL_TASK_STACK_SIZE	512
#define MOTOR_CONTROL_P_GAIN			0.8f
#define MOTOR_CONTROL_I_GAIN			0.01f
#define MOTOR_CONTROL_D_GAIN			0.000f


/************************************************
 * 軌道追従制御の設定
 ***********************************************/
#define TRACKING_CONTROL_TASK_PRIORITY		2
#define TRACKING_CONTROL_TASK_PERIOD		5
#define TRACKING_CONTROL_TASK_PERIOD_SEC	((float)TRACKING_CONTROL_TASK_PERIOD/1000.0f)
#define TRACKING_CONTROL_TASK_STACK_SIZE	512
#define TRACKING_CONTROL_OMEGA_FORWARD_GAIN	1.05f
#define TRACKING_CONTROL_X_P_GAIN			10.0f
#define TRACKING_CONTROL_X_D_GAIN			20.0f
#define TRACKING_CONTROL_Y_P_GAIN			10.0f
#define TRACKING_CONTROL_Y_D_GAIN			0.001f
#define TRACKING_CONTROL_ANGLE_P_GAIN		10.0f
#define TRACKING_CONTROL_ANGLE_I_GAIN		0.1f
#define TRACKING_CONTROL_ANGLE_D_GAIN		0.0f
#define TRACKING_CONTROL_WALL_FILTER_GAIN	0.02f //小さいほど平滑化される
#define TRACKING_CONTROL_WALL_TO_OMEGA_GAIN	0.001f
#define TRACKING_CONTROL_WALL_TO_X_GAIN		(0.01f/1000.0f/1000.0f)


/************************************************
 * Top Taskの設定
 ***********************************************/
#define TOP_TASK_PRIORITY		3
#define TOP_TASK_STACK_SIZE		1024*4


/************************************************
 * LED点滅 Taskの設定
 ***********************************************/
#define BLINK_LED_TASK_PRIORITY		4
#define BLINK_LED_TASK_STACK_SIZE	128


#endif /* CONFIG_H_ */

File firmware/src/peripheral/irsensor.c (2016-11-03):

/*
 * irsensor.c
 *
 *  Created on: 2016/10/20
 *      Author: idt12312
 */

#include "stm32f4xx_conf.h"
#include "irsensor.h"

#include "FreeRTOS.h"
#include "semphr.h"


// 赤外線LEDを駆動するPWMの周波数
// 10kHz = 84MHz / 8400
#define IRSENSOR_PWM_TIM_PERIAD 8400

#define IRSENSOR_PWM_DUTY 0.5f

// パルス何個分を計測するか
#define N_PULSE 4

// PWMの１周期中に何回サンプルするか
// これにPWM周波数をかけるとADCのサンプリング周波数になる
#define N_MUL 16


// 一回の計測で1chあたり何回サンプルするか
#define N_SAMPLE N_MUL*N_PULSE

// ADCの結果を保存するバッファのサイズ
#define N_ADC_CNT N_SAMPLE*2

// ADCトリガ用タイマの周期
#define ADC_TRIG_TIM_PERIOD IRSENSOR_PWM_TIM_PERIAD/N_MUL

// DMAの割り込み優先度
#define ADC_DMA_IRQ_PRIORITY	6

typedef enum {
	SENSOR13,
	SENSOR24
} Sensor;


// adc_result[i]の
// 前半部分はch1と3で, 上位16bitがch3, 下位16bitがch1
// 後半部分はch2と4で, 上位16bitがch4, 下位16bitがch2
// ダブルバッファリングをするので二つ確保してある
static uint32_t adc_result[2][N_ADC_CNT];

static bool measuring;
static Sensor measuring_sensor;

static xSemaphoreHandle data_ready_semaphore;


static void pwm_init()
{
	// GPIOを設定
	RCC_AHB1PeriphClockCmd(RCC_AHB1Periph_GPIOA, ENABLE);

	GPIO_InitTypeDef  GPIO_InitStructure;
	GPIO_InitStructure.GPIO_Pin =  GPIO_Pin_6 | GPIO_Pin_7;
	GPIO_InitStructure.GPIO_Speed = GPIO_Speed_50MHz;
	GPIO_InitStructure.GPIO_Mode = GPIO_Mode_AF;
	GPIO_InitStructure.GPIO_OType = GPIO_OType_PP;
	GPIO_InitStructure.GPIO_PuPd = GPIO_PuPd_NOPULL;
	GPIO_Init(GPIOA, &GPIO_InitStructure);

	// DACのピンは入力にしとく
	GPIO_InitStructure.GPIO_Pin =  GPIO_Pin_4 | GPIO_Pin_5;
	GPIO_InitStructure.GPIO_Speed = GPIO_Speed_50MHz;
	GPIO_InitStructure.GPIO_Mode = GPIO_Mode_IN;
	GPIO_InitStructure.GPIO_OType = GPIO_OType_OD;
	GPIO_InitStructure.GPIO_PuPd = GPIO_PuPd_NOPULL;
	GPIO_Init(GPIOA, &GPIO_InitStructure);

	GPIO_PinAFConfig(GPIOA, GPIO_PinSource6, GPIO_AF_TIM3);
	GPIO_PinAFConfig(GPIOA, GPIO_PinSource7, GPIO_AF_TIM3);


	// PWMを出すTIMを設定
	// TimeBaseではPWMの周期を設定
	RCC_APB1PeriphClockCmd(RCC_APB1Periph_TIM3, ENABLE);

	TIM_TimeBaseInitTypeDef  TIM_TimeBaseStructure;
	TIM_TimeBaseStructure.TIM_Period = IRSENSOR_PWM_TIM_PERIAD - 1;
	TIM_TimeBaseStructure.TIM_Prescaler = 0;
	TIM_TimeBaseStructure.TIM_ClockDivision = 0;
	TIM_TimeBaseStructure.TIM_CounterMode = TIM_CounterMode_Up;
	TIM_TimeBaseStructure.TIM_RepetitionCounter = 0;
	TIM_TimeBaseInit(TIM3, &TIM_TimeBaseStructure);

	// 各PWM出力ピンに対応するコンペアレジスタを設定
	// ここでは共に出力0に設定
	// pwm_startでPWMモードに設定をしている
	TIM_OCInitTypeDef  TIM_OCInitStructure;
	TIM_OCInitStructure.TIM_OCMode = TIM_OCMode_PWM1;
	TIM_OCInitStructure.TIM_OutputState = TIM_OutputState_Enable;
	TIM_OCInitStructure.TIM_OutputNState = TIM_OutputNState_Disable;
	TIM_OCInitStructure.TIM_OCPolarity = TIM_OCPolarity_High;
	TIM_OCInitStructure.TIM_OCIdleState = TIM_OCIdleState_Reset;
	TIM_OCInitStructure.TIM_Pulse = 0;
	TIM_OC1Init(TIM3, &TIM_OCInitStructure);
	TIM_OC2Init(TIM3, &TIM_OCInitStructure);

	// CCRの値はTIMのoverflowイベントとは非同期で反映される
	TIM_OC1PreloadConfig(TIM3, TIM_OCPreload_Disable);
	TIM_OC2PreloadConfig(TIM3, TIM_OCPreload_Disable);
}


static void pwm_start(Sensor sensor)
{
	if (sensor == SENSOR13) {
		TIM3->CCR1 = (uint16_t)(IRSENSOR_PWM_TIM_PERIAD * IRSENSOR_PWM_DUTY);
		TIM3->CCR2 = 0;
	}
	else {
		TIM3->CCR1 = 0;
		TIM3->CCR2 = (uint16_t)(IRSENSOR_PWM_TIM_PERIAD * IRSENSOR_PWM_DUTY);
	}

	// PWM出力開始
	TIM3->CNT = 0;
	TIM_Cmd(TIM3, ENABLE);
}


static void pwm_stop()
{
	TIM3->CCR1 = 0;
	TIM3->CCR2 = 0;
	TIM_Cmd(TIM3, DISABLE);
}


static void adc_init()
{
	// GPIOをアナログ入力に設定
	GPIO_InitTypeDef  GPIO_InitStructure;

	RCC_AHB1PeriphClockCmd(RCC_AHB1Periph_GPIOC, ENABLE);
	GPIO_InitStructure.GPIO_Pin =  GPIO_Pin_4 | GPIO_Pin_5;
	GPIO_InitStructure.GPIO_Mode = GPIO_Mode_AN;
	GPIO_InitStructure.GPIO_PuPd = GPIO_PuPd_NOPULL;
	GPIO_Init(GPIOC, &GPIO_InitStructure);

	RCC_AHB1PeriphClockCmd(RCC_AHB1Periph_GPIOB, ENABLE);
	GPIO_InitStructure.GPIO_Pin =  GPIO_Pin_0 | GPIO_Pin_1;
	GPIO_InitStructure.GPIO_Mode = GPIO_Mode_AN;
	GPIO_InitStructure.GPIO_PuPd = GPIO_PuPd_NOPULL;
	GPIO_Init(GPIOB, &GPIO_InitStructure);


	// ADCのトリガとなるタイマの設定
	RCC_APB1PeriphClockCmd(RCC_APB1Periph_TIM2 , ENABLE);

	TIM_TimeBaseInitTypeDef  TIM_TimeBaseStructure;
	TIM_TimeBaseStructure.TIM_Period = ADC_TRIG_TIM_PERIOD-1;
	TIM_TimeBaseStructure.TIM_Prescaler = 0;
	TIM_TimeBaseStructure.TIM_ClockDivision = 0;
	TIM_TimeBaseStructure.TIM_CounterMode = TIM_CounterMode_Up;
	TIM_TimeBaseStructure.TIM_RepetitionCounter = 0;
	TIM_TimeBaseInit(TIM2, &TIM_TimeBaseStructure);


	TIM_OCInitTypeDef  TIM_OCInitStructure;
	TIM_OCInitStructure.TIM_OCMode = TIM_OCMode_PWM1;
	TIM_OCInitStructure.TIM_OutputState = TIM_OutputState_Enable;
	TIM_OCInitStructure.TIM_OutputNState = TIM_OutputNState_Disable;
	TIM_OCInitStructure.TIM_OCPolarity = TIM_OCPolarity_High;
	TIM_OCInitStructure.TIM_OCIdleState = TIM_OCIdleState_Reset;
	TIM_OCInitStructure.TIM_Pulse = ADC_TRIG_TIM_PERIOD-2;
	TIM_OC2Init(TIM2, &TIM_OCInitStructure);


	// ADCの設定
	// TIM2 TRGOをトリガに変換をする
	// チャンネルの設定はadc_startで
	RCC_APB2PeriphClockCmd(RCC_APB2Periph_ADC1, ENABLE);
	RCC_APB2PeriphClockCmd(RCC_APB2Periph_ADC2, ENABLE);

	ADC_InitTypeDef  ADC_InitStructure;
	ADC_InitStructure.ADC_Resolution = ADC_Resolution_12b;
	ADC_InitStructure.ADC_ScanConvMode = ENABLE;
	ADC_InitStructure.ADC_ContinuousConvMode = DISABLE;
	ADC_InitStructure.ADC_ExternalTrigConv = ADC_ExternalTrigConv_T2_CC2;
	ADC_InitStructure.ADC_ExternalTrigConvEdge = ADC_ExternalTrigConvEdge_Rising;
	ADC_InitStructure.ADC_DataAlign = ADC_DataAlign_Right;
	ADC_InitStructure.ADC_NbrOfConversion = 1;
	ADC_Init(ADC1, &ADC_InitStructure);
	ADC_Init(ADC2, &ADC_InitStructure);

	// ADCのクロック 21MHz = 84MHz / 4
	// デュアルモードでADC1,2を同時に使う
	// DMA access mode 2(32bit幅で転送し, 上位16bitがADC2, 下位16bitがADC1)
	ADC_CommonInitTypeDef ADC_CommonInitStructure;
	ADC_CommonInitStructure.ADC_Mode = ADC_DualMode_RegSimult;
	ADC_CommonInitStructure.ADC_Prescaler = ADC_Prescaler_Div4;
	ADC_CommonInitStructure.ADC_DMAAccessMode = ADC_DMAAccessMode_2;
	ADC_CommonInitStructure.ADC_TwoSamplingDelay = ADC_TwoSamplingDelay_5Cycles;
	ADC_CommonInit(&ADC_CommonInitStructure);

	// ADC1,2の変換が両方とも終わったらDMAで転送
	ADC_MultiModeDMARequestAfterLastTransferCmd(ENABLE);

	ADC_Cmd(ADC1, ENABLE);
	ADC_Cmd(ADC2, ENABLE);


	// ADCの変換結果を転送するDMAの設定
	// ADCをdualモードで使っているので、ADCx.DRではなくADC.CDRのデータを転送する
	RCC_AHB1PeriphClockCmd(RCC_AHB1Periph_DMA2, ENABLE);
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

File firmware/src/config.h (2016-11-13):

/*
 * config.h
 *
 *  Created on: 2016/10/31
 *      Author: idt12312
 */

#ifndef CONFIG_H_
#define CONFIG_H_


/************************************************
 * デバッグ用の設定
 ***********************************************/
#define USE_GYRO	1


/************************************************
 * マシンの物理的パラメータ
 ***********************************************/
#define WHEEL_RADIUS	0.01237f
// 中心からタイヤまでの距離
#define TREAD_WIDTH 	0.03289f
#define ENC_CNT_PER_ROT	(1024*4*4)
#define MOTOR_VOLTAGE	7.6f


/************************************************
 * マシンの走行パラメータ
 ***********************************************/
#define STRAIGHT_DEFAULT_VELOCITY		0.1f
#define STRAIGHT_MAX_VELOCITY			0.2f
#define STRAIGHT_ACCERALATION			1.0f
#define PIVOT_ROTATION_VELOCITY			3.0f
#define PIVOT_ROTATION_ACCERALATION		15.0f
#define SLALOM_VELOCITY					0.1f
#define SLALOM_ROTATION_VELOCITY		1.5f
#define SLALOM_ROTATION_ACCERALATION	10.0f


/************************************************
 * フィールドの物理的パラメータ
 ***********************************************/
#define BLOCK_SIZE	0.18f


/************************************************
 * バッテリー監視タスクの設定
 ***********************************************/
#define BATTERY_MONITOR_TASK_PRIORITY	3
#define BATTERY_MONITOR_TASK_PERIOD		2000
#define BATTERY_MONITOR_TASK_STACK_SIZE 256
#define BATTERY_MONITOR_AVE_CNT			5
#define BATTERY_MONITOR_ALERT_THREHOLD	7.4f
#define ADC_TO_BATTERY_VOLTAGE(x)		((float)x / 4096.0f * 3.3f * 3.0f)


/************************************************
 * 壁検出タスクの設定
 ***********************************************/
#define WALL_DETECT_TASK_PRIORITY		2
#define WALL_DETECT_TASK_PERIOD			5
#define WALL_DETECT_TASK_STACK_SIZE		1024
#define WALL_DETECT_RL_THREHOLD			3300
#define WALL_DETECT_FRONT_THRETHOLD_NOSIDE		3500
#define WALL_DETECT_FRONT_THRETHOLD_WITH_SIDE		3600
#define WALL_DETECT_CNT					4


/************************************************
 * モータ制御(姿勢制御)タスクの設定
 ***********************************************/
#define MOTOR_CONTROL_TASK_PRIORITY		1
#define MOTOR_CONTROL_TASK_PERIOD		1
#define MOTOR_CONTROL_TASK_PERIOD_SEC	((float)MOTOR_CONTROL_TASK_PERIOD/1000.0f)
#define MOTOR_CONTROL_TASK_STACK_SIZE	512


/************************************************
 * 軌道追従タスクの設定
 ***********************************************/
#define TRACKING_CONTROL_TASK_PRIORITY		2
#define TRACKING_CONTROL_TASK_PERIOD		5
#define TRACKING_CONTROL_TASK_PERIOD_SEC	((float)TRACKING_CONTROL_TASK_PERIOD/1000.0f)
#define TRACKING_CONTROL_TASK_STACK_SIZE	512
#define TRACKING_CONTROL_OMEGA_FORWARD_GAIN	1.05f
#define WALL_COMPENSATOR_P_GAIN				(0.8f/1000.0f/1000.0f)

#endif /* CONFIG_H_ */

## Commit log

2016-09-29 基板データを追加
    [body.dxf, debug_adaptor.sch, imu.sch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]
2016-09-29 eclipseのプロジェクトを作成
2016-09-29 FPU・内部発振を有効化
2016-10-02 UART(DMA使用)を扱う部分を実装
2016-10-02 ロータリエンコーダの読み取り部分を実装
2016-10-02 モータ用PWMの操作部分を実装
2016-10-02 MPU6500とSPIを実装 Z軸周りの角加速度だけ取得できる
2016-10-02 ヘッダをincludeに移動
2016-10-02 READMEを追加
2016-10-22 MPU6500周りを修正 ・CSの操作 ・MPU6500のレジスタのアドレスの指定方法 ・MPU6500から読み取った角速度データの解釈の仕方
    [mpu6500.c]
2016-10-22 Tickを実装
2016-10-25 エンコーダの読み取り部分を修正
2016-10-25 LEDとボタンの操作部分を実装
2016-10-25 モータの操作部分を実装
2016-10-25 標準出力をUARTに流すように修正
2016-10-25 バッテリー電圧計測部分を実装
2016-10-25 赤外線の発光受光部分を実装
2016-10-25 各機能のテスト
2016-10-25 ソースのディレクトリを変更
2016-10-25 FreeRTOSを導入 MPU6500の初期化時にTick_waitを使っているが、RTOSを起動するまで使えないのでfor分で待つように変更
2016-10-28 CMSISのヘッダを最新版に差し替え & DSPライブラリを追加
2016-10-29 直交復調を実装
2016-10-29 C++のコンパイルオプションでRTTIと例外を無効化
2016-10-29 赤外線LED用のLEDの設定が間違っていたので修正 ・PWM周波数が2倍になっていたので修正 ・DMAの半分送信割り込みが起こったとき、点滅させるLEDを切り替え忘れていたので修正
2016-10-29 直交復調のテスト
2016-11-01 ジャイロセンサのオフセットのキャリブレーションを実装
2016-11-03 SPI通信部分を分離し、DMAを使った実装にした DMAの転送が終了するまではセマフォを使ってブロックできる
2016-11-03 割り込み優先度を調整
2016-11-03 バッテリー監視タスクを実装 バッテリー監視用ADCの設定を変更
2016-11-03 QuadratureDemodulatorを修正 ・計算結果用のクラスを作ってそれを返すようにした ・回転因子をunique_ptrで実装
2016-11-03 壁センサのためにサンプリングしている時、セマフォでブロックする実装に変更
2016-11-03 壁のあるなしを判定するタスクを実装
2016-11-03 エンコーダのデータのやり取りを構造体を通して行うように変更
2016-11-03 モータ入力を電圧で指定できるようにした
2016-11-03 モータの制御タスクを実装 ・車体の並進速度・角速度を目標値として与える ・モータにかける電圧(duty比)が制御入力
2016-11-07 起動直後にバッテリー電圧を計測してバッテリーの残量を判定するのをやめた コンデンサに充電しきる前に計測されてしまい、低く出てしまうから
2016-11-07 オドメトリを実装 & 動作確認
2016-11-09 PIDコントローラのAPIを変更
2016-11-09 ジャイロのオフセットキャリブレーションを修正
2016-11-09 Velocityの足し算引き算を実装
2016-11-09 軌道の生成部分を実装 テスト用に直進と超信地旋回を実装
2016-11-09 タイヤ径とドレッド径を実測により調整
2016-11-09 座標の取り方を変えた ・ロボット(ローカル)座標系は進行方向がy座標 ・ワールド座標系のx軸 -> ロボット座標系のx軸の角度がθ
2016-11-09 軌道追従コントローラを実装
2016-11-09 軌道追従制御のタスクを実装 直進・超信地旋回ができることを確認
2016-11-11 スラロームを実装
2016-11-11 C++の動的リンクを使わない設定を追加
2016-11-11 複数のTrajectoryを連続して実行できるように修正 Trajectoryをqueueから取り出すごとにodometoryをリセットしている
2016-11-11 直進、超信地旋回、スラローム旋回、それぞれ移動量などをパラメータで与えられるように修正
2016-11-11 Trajectoryを切り替えるごとに今いる位置の分だけあらかじめカウンタを進めるように修正 目標点を超えた状態でTrajectoryを切り替えると逆方向に戻ろうとしてしまうため
2016-11-12 角度の計測のみにgyroを使い、機体の速度制御はエンコーダの情報のみを用いる gyroから得た角速度情報を機体の速度制御に用いると振動的になるため
2016-11-12 軌道の追従制御において、あらかじめ計画した目標速度のフィードフォワード入力のゲインを設定できるようにした スラロームの際に大回りになってしまうため
2016-11-12 軌道追従の制御のパラメータをチューニング
2016-11-13 前壁センサの判定に使う閾値を左右に壁があるときとないときで変えられるように修正
2016-11-13 直進時に左右の壁を使ってx座標を修正する機能を追加
2016-11-13 機体の角度を計算をジャイロから得た角速度を使うかエンコーダから得た角速度を使うかを切り替えられるようにした 普段はジャイロを使うが、タイヤを浮かせてデバッグするときにはエンコーダを使うといい
2016-11-13 1つのTrajectoryが終了したときの処理の追加
2016-11-13 バックをする時は目標点のx座標を追従するために入力する角速度の方向を逆にした
2016-11-14 バックしてマシンの尻を壁に当てて補正するのを実装 Trajectoryのset_adjust_odometry_flagをたてるとそのTrajectoryを実行後に座標(y,theta)をリセットする
2016-11-14 Trajectory -> Motion にrename
2016-11-14 デバッグのための設定を追加
2016-11-14 モータコントローラ、軌道追従制御コントローラの制御パラメータはコンストラクタの引数で渡すのではなく、 コンストラクタに直接うめこむ実装に変更
2016-11-14 クラスの宣言と実装を分けた
2016-11-14 ソースディレクトリを整理
2016-11-16 各タスクをクラスにまとめた & motionが切り替わる時のodometoryのリセット処理を修正
2016-11-16 SPIの通信速度を切り替えられるようにし、初期設定は低速、データの読み取りは高速に通信するように変更
2016-11-16 ボタンを監視するタスクを追加
2016-11-16 ロボットの機械的なパラメータの名前を変更
2016-11-16 ・壁の判定を少し手前で行うように変更 ・壁当て補正を修正 ・区画が切り替わる時の目標値との誤差の計算を修正 ・Motionの終了通知
    [MotionControlTask.cpp, TopTask.cpp, config.h]
2016-11-16 ジャイロのゲインを変更
2016-11-16 超信地旋回の角速度のフィードフォワードのゲインを設定できるようにした
2016-11-16 探索アルゴリズムをsubmoduleとして取り込んだ
2016-11-16 ビルド設定に探索ライブラリを追加
2016-11-17 コンパイルオプションを追加
2016-11-17 タスクのスタックを調整
2016-11-17 PIDControllerとOdometryにおける微分のための前回値のリセット処理を追加
2016-11-17 Motion周りの終わりの処理を修正
2016-11-17 区画の終了判定を修正
2016-11-17 探索部分を実装 各種パラメータを調整
2016-11-17 Motionにパラメータとして与えられるようにした
2016-11-17 最速走行の動作を実装 ・最短走行と探索走行で走行パラメータをわけた ・手をかざすとスタートする ・LEDを制御
2016-11-18 LEDの点滅タスクを点滅パターンをいろいろいじれるように修正
2016-11-18 横壁補正を実装
2016-11-18 スタートするための操作をいろいろ実装 手をかざすとスタートする
2016-11-18 パラメータを調整
2016-11-18 片側にしか壁がない時は壁の補正をしない
2016-11-18 最速走行まわりのバグを修正
2016-11-19 gitignoreを追加
2016-11-22 軌道をプロットするMATLABスクリプトを追加
2016-11-24 回路図を修正 ・赤外線LEDの発光回路にpull down抵抗を追加 ・赤外線LEDの発光回路の電流制限抵抗の値を変更
    [ir_receiver.sch, ir_transmitter.sch, motor.sch]
2016-11-27 実体配線図に抵抗を追加
    [micromouse2016.kicad_pcb]
2016-12-10 READMEを追記
    [imu.sch, ir_receiver.sch, ir_transmitter.sch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]
2017-02-28 README.mdの数式をcodecogsで生成した画像で表示するようにした
2017-02-28 README.mdの数式で、inlineのものはinline指定にした
2017-02-28 README.mdの数式へのリンクをmarkdown形式で書いた
2017-02-28 Revert "README.mdの数式へのリンクをmarkdown形式で書いた"
    This reverts commit 1478dd8bda064d6265e28aa823ffcd6b57f4bd83.
2019-02-09 壁センサに関するまとめ文章を追加
